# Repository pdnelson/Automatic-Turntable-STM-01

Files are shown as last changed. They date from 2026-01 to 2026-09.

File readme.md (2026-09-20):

# The Statimatic STM-01

This is (going to be) a fully-automatic, modular turntable, called the Statimatic STM-01. The development of this turntable is being documented in the following YouTube series: [https://www.youtube.com/watch?v=k4UXI1rkMYs\&list=PL\_8A3xK4AntYpp8yXHuAbhb6lULQ2ivFA](https://www.youtube.com/playlist?list=PL_8A3xK4AntYpp8yXHuAbhb6lULQ2ivFA)

At this time, an AR-XA turntable (left) is being used as the fill-in "turntable" for the STM-01 (right) during development. Eventually, the STM-01 will get its own turtable


## Electronics
This project is driven by a Teensy 4.1, three stepper motors to facilitate movement, multiplexers, a shift register, and more! See the `electrical` folder for the full schematic (so far).

Development is progressing on a breadboard, with questionable organization. Eventually, the plan is to etch a custom PCB.


### Schematic

This is the schematic as of 7 June 2026. The objective is to eliminate as much multiplexing as possible at the end of the project, if there are extra Teensy pins left over. The movement stepper demultiplexers (part `SN74LVC1G18DBVR`) will be the first to go. So far, it's looking like I may be able to eliminate these, as their use only saves me 3 pins. I'm not going to pull the trigger on this quite yet, though, because I may encounter other difficulties later on in the project, requiring the use of more pins. It's up in the air at this point.
schematic

## Mechanisms
The automatic tonerm's operation is facilitated by two mechanisms: One for vertical movement (right), and one for horizontal (left).

The vertical axis has a stepper motor driving movement, and a 10k slide potentiometer acting as an absolute encoder, so its position can be monitored.

The horizontal axis has a stepper motor driving horizontal movements, and another stepper motor to engage/disengage the horizontal motor for automatic movement. This mechanism is currently in progress, so there is some more work to do here.



## Previous Turntable
I designed a prototype turntable previously, separately from this repository, around late 2020/early 2021. That prototype lives in [another repository](https://github.com/pdnelson/Automatic-Record-Player). Though I'm no longer working on that project, much of the research, and many of the ideas I experimented with have made their way into this project.

## Planned Features
The built-in features of this turntable will be kept to a minimum, so that development can go more quickly. These features will be able to be expanded using the 5 expansion ports on the back of the turntable.

### Commands
Built-in, the plan is to have two commands: Play and pause. 

"Play" will move the tonearm from the "home" position to the outer edge of the record on the turntable. If the tonearm is not in the home position when "play" is pressed, then it will return home.

"Pause" will lift the tonearm up if it's set down, and set the tonearm down if it's lifted. "Up" movement will be quick, while "down" movement will be slow, to keep records from being damaged.

### Automatic pickup
The turntable will be able to automatically detect the end of the record, and pick itself up when it reaches that point.

### Size Selection
There will be four settings for size selection: 7", 10" and 12". The fourth option is "auto," where the turntable will use the built-in IR sensor to detect the record edge.

One caveat of using "auto" is that the record edge detection will likely be slower, while selecting a specific size will immediately know where to go.

### Speed Selection
There will be four settings for speed selection: 33 1/3, 45, and 78 RPM. The fourth option is "auto," where the turntable will guess, based on the record size, what speed you want.

For 12" records, the 33 1/3 RPM speed will be used. For 10" records, the 78 RPM speed will be used. For 7" records, the 45 RPM speed will be used. If an unusual size is detected, the fallback will be 78 RPM. Why? There are a lot of unusual 78-RPM record sizes out there, so I feel like this one's fitting.

### Statistics
The turntable will maintain a set of statistics that will be able to be viewed on the "Control Panel" module, or "Web Server" module.

These statistics could include:
- Current number of hours/minutes on the stylus
- How many records you've played
  - This will (likely) be counted by size and speed
- How long you've had the turntable powered on
- How long you've had the turntable playing a record

### Modularity

The plan is to allow connection of up to 5 external modules to the turntable, concurrently. The intention is to design the turntable as its own standalone unit, before any modules, so that each module can be designed in isolation.

mod-all-modules-clock

These could be, for example:
- Record flipper
- Record changer
- Second tonearm
- FM transmitter
- Preamp
- Alarm clock
- Remote control
- Splitter (to allow for even more modules!)
- Communication adapter to your favorite vintage computer from the '70s or '80s
- Control panel
- Web server

... And so on!

Got an idea for a module that you think would be cool? Send me a message; I might agree! Though I'm not developing any modules yet, it will be good to build up a nice list of things so I never run out of things to work on.

## Progress

This project has a lot of work that needs done to it. Here's what's been completed so far, and what's left to do:
- [x] Prototype documentation
- [x] Lift mechanism
- [x] Pause/unpause routine
- [x] Design pivoting mechanism
- [x] Design tonearm and headshell assembly
- [x] Connect tonearm to electronics
- [x] Status shift register
- [x] Command Button UI
- [x] Error handling
- [x] External Commands
- [x] Horizontal clutch mechanism
- [x] Horizontal position tracking
- [x] Calibration routine
- [x] "Specific Size" play routine
- [ ] IR record/track detection
- [ ] "Automatic" play routine
- [ ] Automatic homing routine
- [ ] Track forward/backward routine
- [ ] Headshell capacitive touch sensor
- [ ] Audio cut-off circuit
- [ ] Prototype motor/3-phase belt-driven turntable setup
- [ ] Speed monitoring routine
- [ ] Finalized turntable setup (heavy platter and big pulley)
- [ ] Design power supply
- [ ] Save settings when powered off
- [ ] Prototype plinth using plywood
- [ ] Finalized plinth using whatever material I decide to use
- [ ] Design PCB
- [ ] Etch PCB
- [ ] Celebrate a complete STM-01 turntable

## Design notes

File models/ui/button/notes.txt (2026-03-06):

Aluminum rod should be 12mm in length; 1/2" in diameter

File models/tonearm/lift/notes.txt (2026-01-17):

Must use, at most, 15mm layer height for tonearm-lift-attachment

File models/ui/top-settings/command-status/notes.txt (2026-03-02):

Use 0.15mm layers for all parts, except for the bottom mount.

Text:
- Font: Yu Gothic UI Semibold
- Height: 8.00mm
- Extruded: 0.0mm
- Form: Filled
- Weight: Bold

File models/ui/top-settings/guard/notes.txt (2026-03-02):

Model number text:
- Font: Bahnschrift SemiLight SemiConde
- Weight: Regular
- Form: Filled
- Height: 14mm
- Extruded: 0.0mm

Size/speed text:
- Same as above, except height: 5.0mm

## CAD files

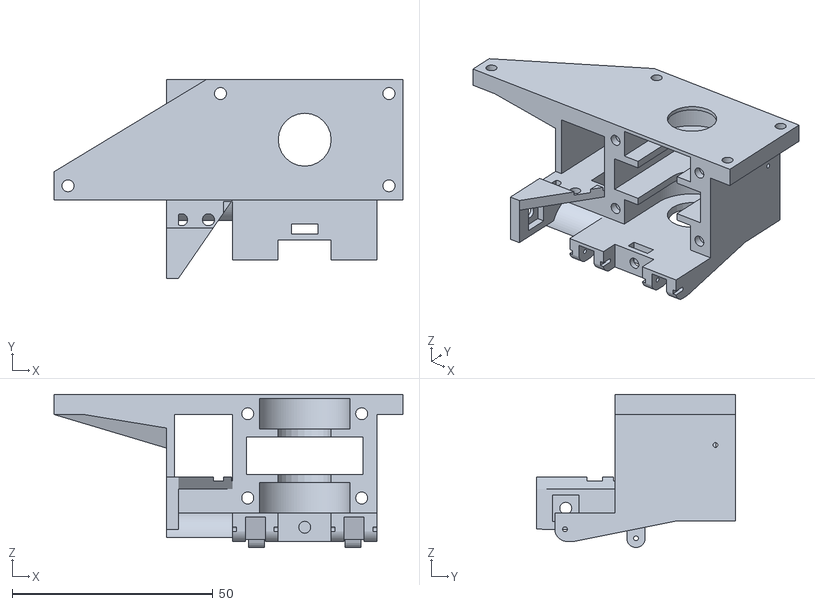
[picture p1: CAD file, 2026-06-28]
models/movement-hub/horizontal/horizontal-hub-main.stl
87.0 x 49.6 x 38.2

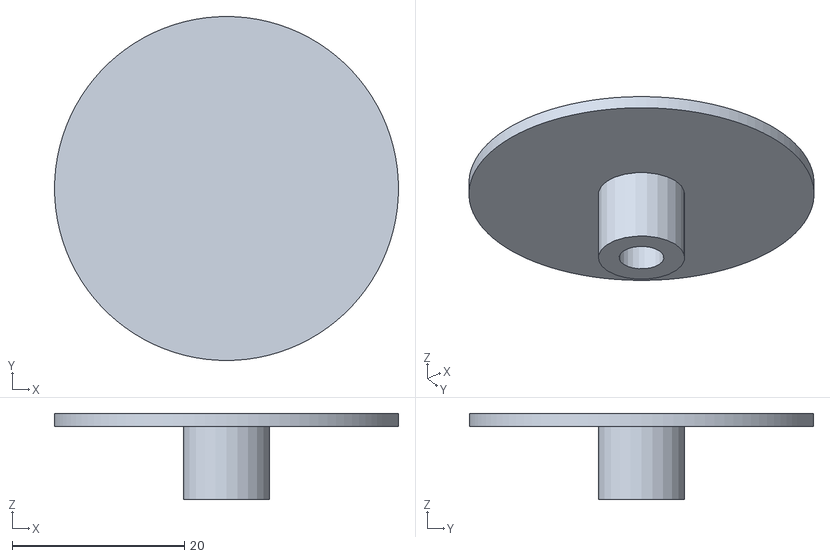
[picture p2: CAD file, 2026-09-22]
models/movement-hub/horizontal/horizontal-hub-motor-disc.stl
40.0 x 40.0 x 10.0

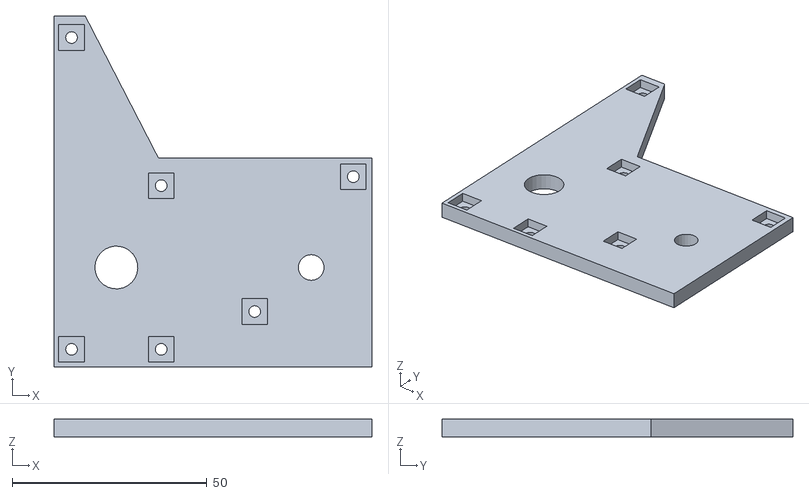
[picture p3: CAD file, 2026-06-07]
models/movement-hub/hub-mount.stl
81.6 x 90.0 x 4.50

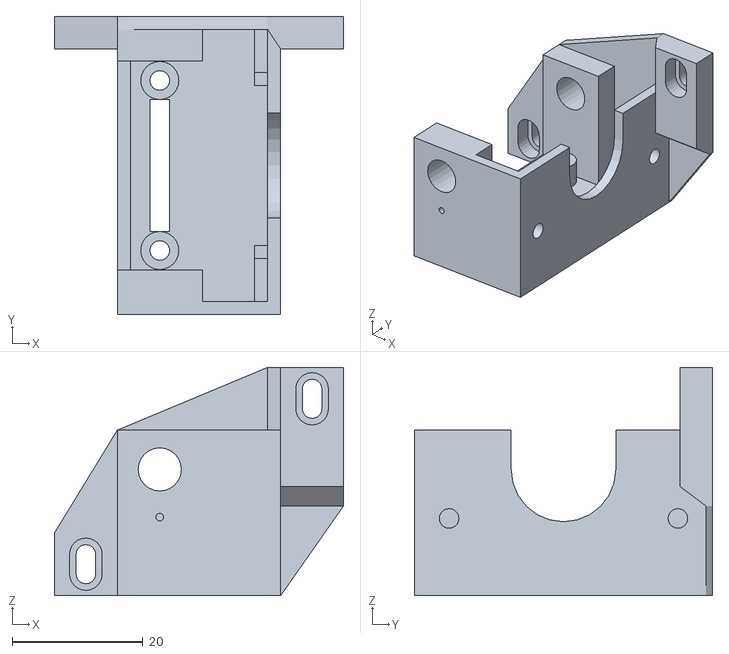
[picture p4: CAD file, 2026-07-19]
models/movement-hub/vertical/vertical-hub.stl
44.2 x 45.6 x 34.9

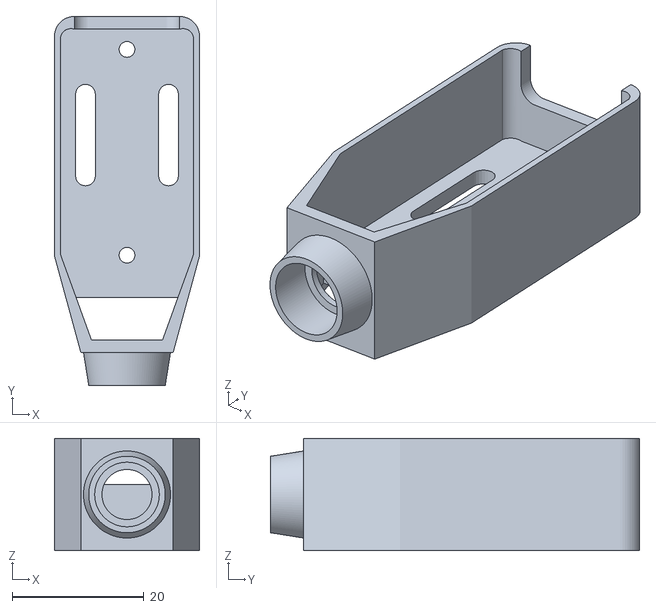
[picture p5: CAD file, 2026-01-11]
models/tonearm/headshell/headshell.stl
22.0 x 56.0 x 17.0

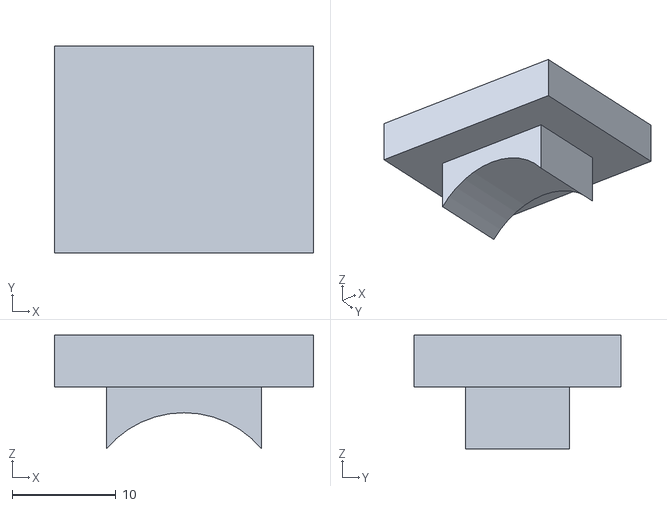
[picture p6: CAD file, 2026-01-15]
models/tonearm/headshell/lift-clamp/lift-clamp-top.stl
25.0 x 20.0 x 11.0

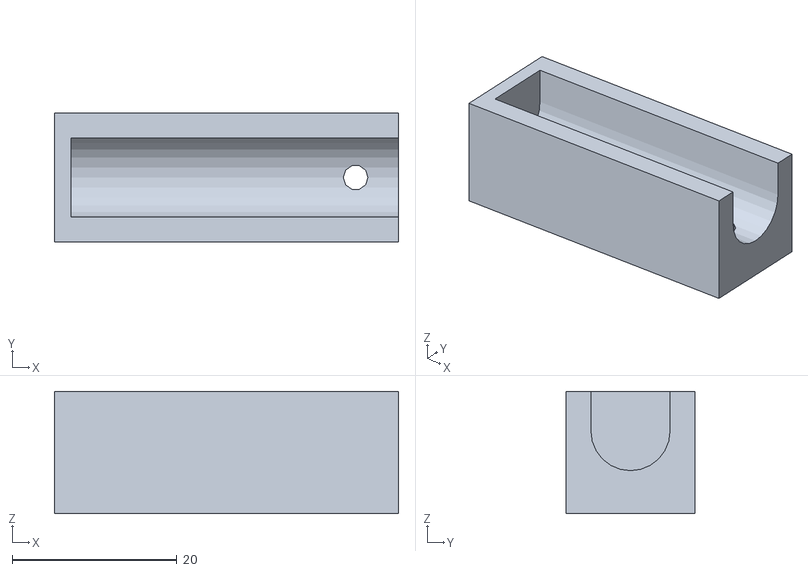
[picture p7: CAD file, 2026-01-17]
models/tonearm/lift/alignment/tonearm-lift-alignment-tool.stl
41.7 x 15.6 x 14.8

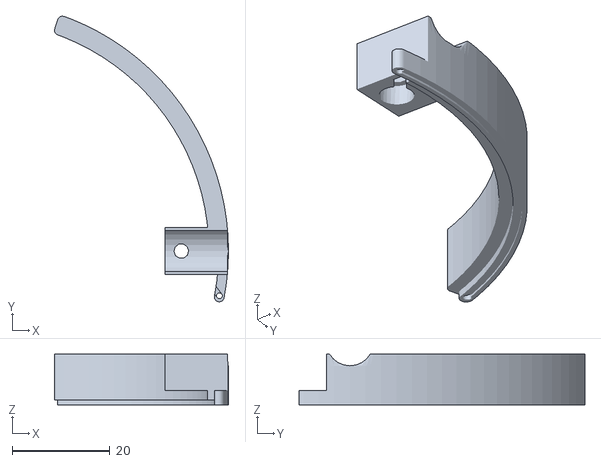
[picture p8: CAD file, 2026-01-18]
models/tonearm/lift/tonearm-lift-attachment.stl
35.5 x 58.3 x 10.4

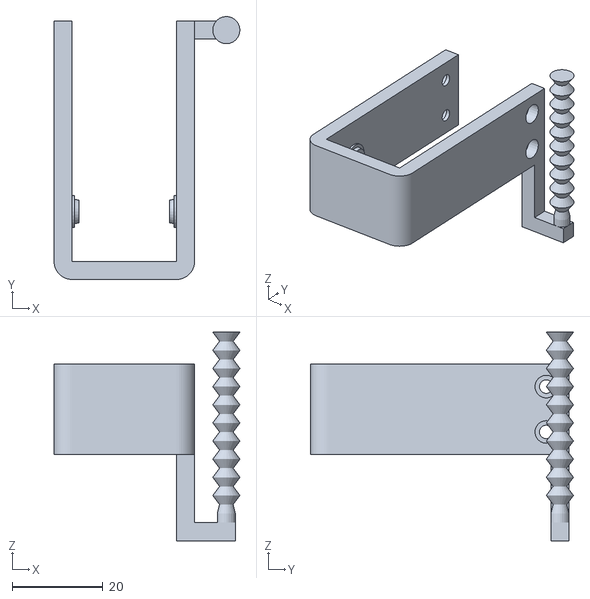
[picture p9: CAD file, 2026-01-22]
models/tonearm/pivot-mechanism/pivot-tonearm-holder.stl
41.0 x 58.0 x 46.0

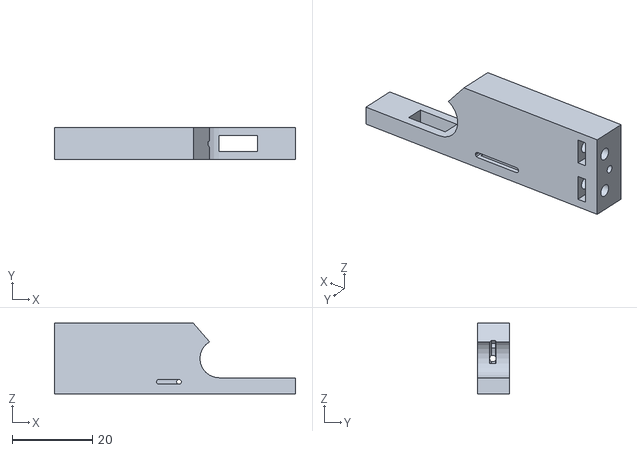
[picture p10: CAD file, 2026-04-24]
models/tonearm/rest/tonearm-rest.stl
60.0 x 7.90 x 17.6

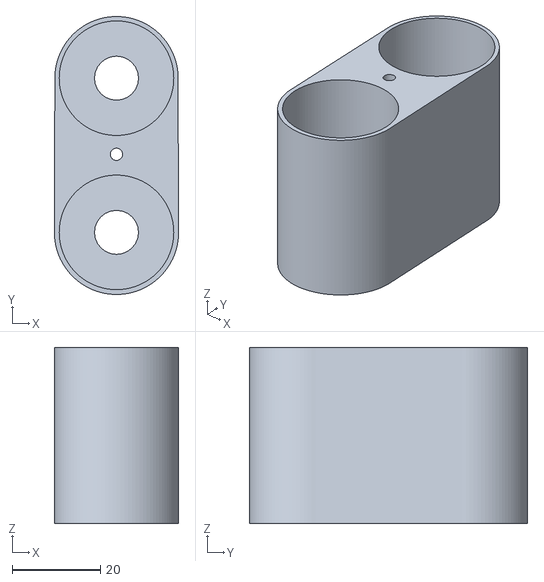
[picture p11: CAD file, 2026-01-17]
models/tonearm/weight/tonearm-weight.stl
28.2 x 63.1 x 40.0

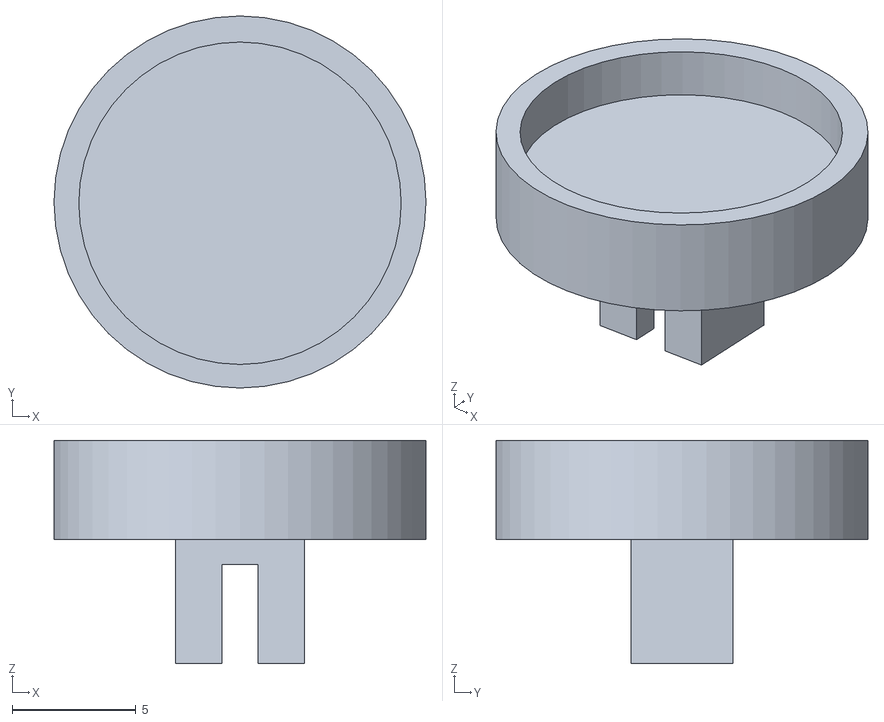
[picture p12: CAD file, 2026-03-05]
models/ui/button/button.stl
15.0 x 15.0 x 9.00

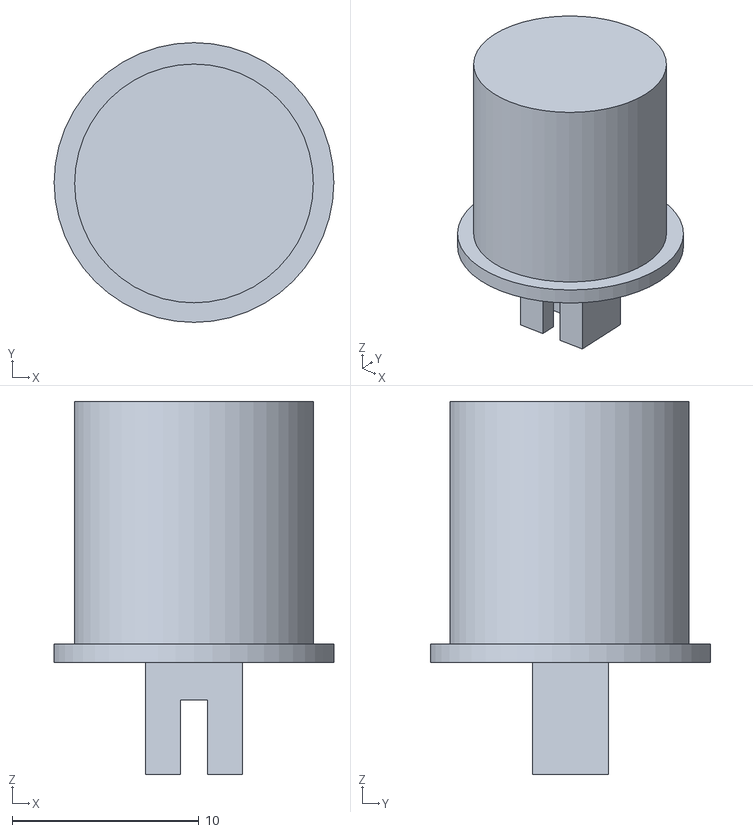
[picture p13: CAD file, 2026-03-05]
models/ui/button/prototype/button-prototype.stl
15.0 x 15.0 x 20.0

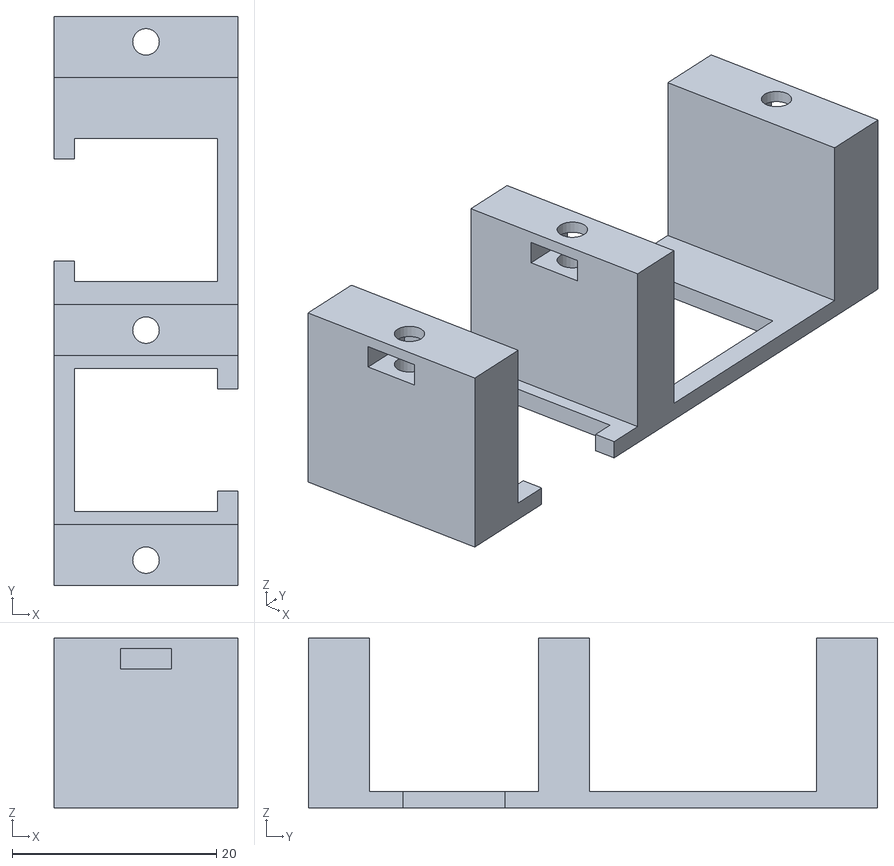
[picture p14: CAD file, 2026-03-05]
models/ui/top-settings/command-status/button/command-button-holder.stl
18.0 x 55.7 x 16.6

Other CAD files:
models/ui/top-settings/command-status/command-top-display-mount.stl
models/ui/top-settings/command-status/display/command-display-power.stl
models/ui/top-settings/guard/prototype/ui-guard-prototype-pt-2.stl
models/ui/top-settings/guard/ui-guard-without-text.dxf
models/movement-hub/horizontal/brackets-positioners/horizontal-hub-bearing-bracket.skp
models/movement-hub/horizontal/brackets-positioners/horizontal-hub-bearing-bracket.stl
models/movement-hub/horizontal/brackets-positioners/horizontal-hub-shaft-positioner.skp
models/movement-hub/horizontal/brackets-positioners/horizontal-hub-shaft-positioner.stl
models/movement-hub/horizontal/brackets-positioners/screw-contact-pad.skp
models/movement-hub/horizontal/brackets-positioners/screw-contact-pad.stl
models/movement-hub/horizontal/hinge-washer.skp
models/movement-hub/horizontal/hinge-washer.stl
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

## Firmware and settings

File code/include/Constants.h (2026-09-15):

#ifndef CONSTANTS_H

#define VERSION_MAJOR 0
#define VERSION_MINOR 0
#define VERSION_PATCH 1

#define SERIAL_COMMAND_INIT_KEY 0b00001100
#define SERIAL_COMMAND_MODEL_KEY 0b01101101 // 109 in decimal; 'm' in ASCII
#define SERIAL_COMMAND_CONNECTION_SUCCESS 0b10010010

#define SERIAL_ADVANCED_START_KEY 0b01010111
#define SERIAL_ADVANCED_END_KEY 0b10101000

// The speed at which serial devices should communicate with this turntable.
#define SERIAL_SPEED 115200

// The amount of time, in milliseconds, that a mux button must be held for the `ButtonResult::Held` status to be triggered.
#define BUTTON_HOLD_INTERVAL 2000

// The debounce interval, in milliseconds, for a mux button. I.e. the button cannot be pressed/released more than once within this duration.
#define BUTTON_DEBOUNCE_INTERVAL 20

// The interval, in microseconds, at which to poll the input multiplexer.
#define MUX_POLL_INTERVAL 100

// One seconds, in microseconds.
#define ONE_SECOND_MICROS 1000000

/**
 * Constants related to the pause/unpause commands -------------
 */

// A margin of error for the slide potentiometer "encoders."
#define VERTICAL_ENCODER_TOLERANCE 5

// The number of encoder ticks to move the tonearm down after contact with the lift has been terminated.
#define TICKS_BELOW_RECORD 15 // Set to 0 because the debounce ends up doing this well enough for now (or forever, maybe)

// The pause status is determined by the upper limit, and this is the margin of error for what can be considered "paused"
#define PAUSE_ERROR 50

// The amount of time, in microseconds, that must pass between status changes of the lift.
#define LIFT_DEBOUNCE_MICROS 50000

// The amount of time, in microseconds, that must pass between status changes of the home stand.
#define HOME_DEBOUNCE_MICROS 100000

// The number of steps the vertical stepper must reach before it is considered "stalled".
#define VERTICAL_STALL_STEPS 100

// If the tonearm is hovering over the "home" position, it should go down quickly, as opposed to slowly. This threshold
// helps determine if it's over "home".
#define HOME_THRESHOLD 100



// When the tonearm lifts up toward the center of the platter, it might bounce a little bit. This timeout represents the maximum
// amount of time we allow for the tonearm to bounce, before it should level out.
#define LIFT_BOUNCE_TIMEOUT_MICROS 1750000

// How fast the tonearm should move when lifting.
#define LIFT_UP_SPEED 10

// How fast the tonearm should move when being set down gently.
#define SET_DOWN_SLOWLY 3

// How fast the tonearm should move when being set down quickly.
#define SET_DOWN_QUICKLY 14

/**
 * Constants related to the horizontal movement -----------
 */

// The RPM at which the clutch stepper spins.
#define CLUTCH_SPEED 14

// The number of steps for the clutch to engage, after the limit switch is released.
#define CLUTCH_ENGAGE_STEPS 250

// If the clutch switch doesn't release after this number of steps, the clutch movement failed.
// Similarly, if the clutch switch doesn't press after this value + CLUTCH_ENGAGE_STEPS, the clutch movement failed.
#define CLUTCH_TIMEOUT_STEPS 100

/**
 * Calibration constants
 */

// The number of encoder ticks above the upper threshold that the turntable should move. This value is applied at the time of calibration.
#define VERTICAL_BOUNDARY_UPPER_BUFFER 80

// The number of encoder ticks below the lower threshold that the turntable should move. This value is applied at the time of calibration.
#define VERTICAL_BOUNDARY_LOWER_BUFFER 30

// When zeroing the azimuth encoder, this is the INITIAL offset when beginning the calibration routine. This value is compatible with an incorrect polarity,
// because it's pretty close to the middle of both bounds.
#define HOME_ZERO_OFFSET 8000

/**
 * Below here are Serial aliases to make it easier to identify the STM-01's serial ports on the back in the code.
 */

#define STM_SERIAL_USB Serial
#define STM_SERIAL_1 Serial1
#define STM_SERIAL_2 Serial2
#define STM_SERIAL_3 Serial7
#define STM_SERIAL_4 Serial8
#define STM_SERIAL_5 Serial3

#endif

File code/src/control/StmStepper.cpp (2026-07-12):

#include <StmStepper.h>
#include <Arduino.h>
#include <Pin.h>
#include <AzimuthDirection.h>
#include <StmStepperResult.h>

StmStepper::StmStepper(Pin pin1, Pin pin2, Pin pin3, Pin pin4) {
    this->pin1 = pin1;
    this->pin2 = pin2;
    this->pin3 = pin3;
    this->pin4 = pin4;

    pinMode(pin1, OUTPUT);
    pinMode(pin2, OUTPUT);
    pinMode(pin3, OUTPUT);
    pinMode(pin4, OUTPUT);
}

void StmStepper::setSpeed(uint8_t speedRpm) {
    this->topSpeedTimeBetweenStepsMicros = 60000000L / STEPPER_STEPS_PER_REVOLUTION / speedRpm;
}

void StmStepper::setDirection(int8_t direction) {
    this->direction = direction;
}

void StmStepper::setRampUpEncoderTicks(uint16_t rampUp) {
    rampUpEncoderTicks = rampUp;
}

void StmStepper::setRampDownEncoderTicks(uint16_t rampDown) {
    rampDownEncoderTicks = rampDown;
}

void StmStepper::setEncoderRange(uint16_t start, uint16_t end, uint8_t tolerance) {
    startEncoderPosition = start;
    destinationEncoderPosition = end;
    destinationEncoderPositionTolerance = tolerance;
    direction = (start > end) ? AzimuthDirection::Clockwise : AzimuthDirection::CounterClockwise;
}

StmStepperResult StmStepper::step(unsigned long clockMicros, uint16_t currentEncoderPosition) {
    StmStepperResult result = StmStepperResult();

    // The movement has completed.
    if(movementCompleted(currentEncoderPosition)) {
        result.movementCompleted = true;
    } 
    
    // The movement has not completed, and we need to take a step.
    else {
        uint16_t speed = topSpeedTimeBetweenStepsMicros;

        // Ramp down calculation
        // prioritize ramp down since that's the functional one; ramp up just looks pretty
        if(rampingDown(currentEncoderPosition)) {
            speed = rampDownSpeed(currentEncoderPosition);
        }

        // Ramp up calculation
        else if(rampingUp(currentEncoderPosition)) {
            speed = rampUpSpeed(currentEncoderPosition);
        }

        if(clockMicros - lastStepMicros > speed) {
            performStep();
            lastStepMicros = clockMicros;
            result.stepTaken = true;
        }
    }


    return result;
}

bool StmStepper::stepBlind(unsigned long clockMicros) {
    if(clockMicros - lastStepMicros > topSpeedTimeBetweenStepsMicros) {
        performStep();
        lastStepMicros = clockMicros;
        return true;
    }

    return false;
}

void StmStepper::releaseMotorCurrent() {
    lastStepMicros = 0;
    digitalWrite(pin1, LOW);
    digitalWrite(pin2, LOW);
    digitalWrite(pin3, LOW);
    digitalWrite(pin4, LOW);
}

bool StmStepper::rampingDown(uint16_t currentEncoderPosition) {
    bool movingNegative = destinationEncoderPosition < startEncoderPosition;

    return (movingNegative && currentEncoderPosition - rampDownEncoderTicks < destinationEncoderPosition) ||
            (!movingNegative && currentEncoderPosition + rampDownEncoderTicks > destinationEncoderPosition);
}

bool StmStepper::rampingUp(uint16_t currentEncoderPosition) {
    bool movingNegative = destinationEncoderPosition < startEncoderPosition;

    return (movingNegative && currentEncoderPosition > startEncoderPosition - rampUpEncoderTicks) ||
            (!movingNegative && currentEncoderPosition < startEncoderPosition + rampUpEncoderTicks);
}

uint16_t StmStepper::rampDownSpeed(uint16_t currentEncoderPosition) {
    uint16_t ticksSoFar = 0; // todo
    return ((STEPPER_MAX_DELAY_BETWEEN_STEPS - topSpeedTimeBetweenStepsMicros) / rampDownEncoderTicks) * ticksSoFar;
}

uint16_t StmStepper::rampUpSpeed(uint16_t currentEncoderPosition) {
    uint16_t ticksSoFar = 0; // todo
    return ((STEPPER_MAX_DELAY_BETWEEN_STEPS - topSpeedTimeBetweenStepsMicros) / rampDownEncoderTicks) * ticksSoFar;
}

bool StmStepper::movementCompleted(uint16_t currentEncoderPosition) {
    bool movingNegative = destinationEncoderPosition < startEncoderPosition;
    
    return (movingNegative && currentEncoderPosition - destinationEncoderPositionTolerance < destinationEncoderPosition) ||
        (!movingNegative && currentEncoderPosition + destinationEncoderPositionTolerance > destinationEncoderPosition);
}

void StmStepper::performStep() {
    currentStep += direction;

    if(currentStep == 4) {
        currentStep = 0;
    } else if(currentStep == -1) {
        currentStep = 3;
    }

    switch (currentStep) {
        case 0:
            digitalWrite(pin1, HIGH);
            digitalWrite(pin2, LOW);
            digitalWrite(pin3, HIGH);
            digitalWrite(pin4, LOW);
            break;
        case 1:
            digitalWrite(pin1, LOW);
            digitalWrite(pin2, HIGH);
            digitalWrite(pin3, HIGH);
            digitalWrite(pin4, LOW);
            break;
        case 2:
            digitalWrite(pin1, LOW);
            digitalWrite(pin2, HIGH);
            digitalWrite(pin3, LOW);
            digitalWrite(pin4, HIGH);
            break;
        case 3:
            digitalWrite(pin1, HIGH);
            digitalWrite(pin2, LOW);
            digitalWrite(pin3, LOW);
            digitalWrite(pin4, HIGH);
            break;
    }
}

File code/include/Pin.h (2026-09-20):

#include <Arduino.h>

#ifndef PIN_H
#define PIN_H

enum Pin : uint8_t {
    Serial1Rx = 0,
    Serial1Tx = 1,
    InputMuxA = 2,
    InputMuxB = 3,
    InputMuxC = 4,
    InputMuxResult = 5,
    MovementStep4 = 6,
    Serial2Rx = 7,
    Serial2Tx = 8,
    MovementStep3 = 9,
    MovementStep2 = 10,
    MovementStep1 = 11,
    HorizontalStep = 12,
    PowerOnStatusIn = 13,
    Serial5Tx = 14,
    Serial5Rx = 15,
    SpeedEncoderB = 16,
    SpeedEncoderA = 17,
    HeadshellPhotoDiode = 18,
    TurntableMotorPhase3 = 19,
    TurntableMotorPhase2 = 20,
    TurntableMotorPhase1 = 21,
    HorizontalClutchSwitch = 22,
    VerticalPosition = 23,
    ReservedI2CScl = 24, // Wire2
    ReservedI2CSda = 25, // Wire2
    HorizontalEnable = 26,
    HorizontalDirection = 27,
    Serial3Rx = 28,
    Serial3Tx = 29,
    Lift = 30,
    HorizontalSleep = 31,
    Serial4Rx = 34,
    Serial4Tx = 35,
    HorizontalClutchStep4 = 38,
    HorizontalClutchStep3 = 39,
    HorizontalClutchStep2 = 40,
    HorizontalClutchStep1 = 41,

    // Unused pins
    Unused32 = 32,
    Unused33 = 33,
    Unused36 = 36,
    Unused37 = 37
};

#endif

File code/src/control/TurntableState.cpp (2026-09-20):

#include <TurntableState.h>
#include <Arduino.h>
#include <CommandResult.h>
#include <Constants.h>
#include <HomeStatus.h>
#include <InputMux.h>
#include <LiftStatus.h>
#include <memory>
#include <MuxPin.h>
#include <Pin.h>
#include <RecordSize.h>
#include <StmBasicStepper.h>
#include <StmShift.h>
#include <TurntableSpeed.h>
#include <CmdError.h>
#include <CmdPause.h>
#include <CmdUnPause.h>
#include <CmdProtoPlay.h>
#include <StmEncoder.h>
#include <ClutchStatus.h>
#include <StmPolarity.h>
#include <CmdGoToPositionH.h>
#include <CmdCalibration.h>

TurntableState::TurntableState() : 
    outputShift(Pin::ReservedI2CSda, Pin::ReservedI2CScl),
    serialComm(this),
    inputMux(Pin::InputMuxA, Pin::InputMuxB, Pin::InputMuxC, Pin::InputMuxResult, MUX_POLL_INTERVAL, BUTTON_HOLD_INTERVAL, BUTTON_DEBOUNCE_INTERVAL),
    verticalStepper(Pin::MovementStep1, Pin::MovementStep3, Pin::MovementStep2, Pin::MovementStep4),
    clutchStepper(Pin::HorizontalClutchStep1, Pin::HorizontalClutchStep3, Pin::HorizontalClutchStep2, Pin::HorizontalClutchStep4),
    azEncoder(Pin::ReservedI2CSda, Pin::ReservedI2CScl),
    horizontalStepper(azEncoder, Pin::HorizontalSleep, Pin::HorizontalEnable, Pin::HorizontalStep, Pin::HorizontalDirection),
    calibration(),
    settings()
{
    pinMode(Pin::VerticalPosition, INPUT);
    pinMode(Pin::HorizontalClutchSwitch, INPUT_PULLUP);

    // Lift
    pinMode(Pin::Lift, INPUT_PULLUP);
    lastLiftStatus = digitalRead(Pin::Lift);

    // Turn on the power LED
    outputShift.setValue(StmShiftPin::LedPower, true);

    settings.load();

    updateCustomSpeed(settings.speed);
    updateSize(settings.size);

    clutchStepper.setSpeed(CLUTCH_SPEED);

    calibration.load();

    azEncoder.setPolarity(calibration.polarityH);
    azEncoder.zeroOutEncoder(calibration.azEncoderOffset);
    horizontalStepper.setPolarity(calibration.hStepperPolarity);
    horizontalStepper.sleep();
}

void TurntableState::monitor() {
    updateClockMicros();
    advanceCounts();
    serialComm.monitor();
    monitorCommandInput();
    executeCommand();
    azEncoder.monitor(clockMicros);

    // Output statuses
    blinkCustomSpeedIndicator();
    outputShift.monitor();
}

void TurntableState::executeCommand() {
    if(currentCommand != nullptr) {
        CommandResult result = currentCommand->execute();

        if(result == CommandResult::Success) {

            // When coming out of the calibration command, go home (if we aren't already there)
            if(currentCommand->getCommandId() == CommandId::Calibration && getHomeStatus() != HomeStatus::Homed) {
                currentCommand = std::make_unique<CmdGoToPositionH>(this, calibration.home, 10, 14);
            } else {
                currentCommand = nullptr;
            }
        } else if(result > CommandResult::Success) {
            currentCommand = std::make_unique<CmdError>(this, result);
        }
    }
}

void TurntableState::rotateSpeed() {
    switch(selectedSpeed) {
        case TurntableSpeed::Rpm33:
            updateSpeed(TurntableSpeed::Rpm45);
            break;
        case TurntableSpeed::Rpm45:
            updateSpeed(TurntableSpeed::Rpm78);
            break;
        case TurntableSpeed::Rpm78:
            updateSpeed(TurntableSpeed::RpmAuto);
            break;
        case TurntableSpeed::RpmAuto:
            updateSpeed(TurntableSpeed::Rpm33);
            break;
        case TurntableSpeed::RpmCustom:
            updateSpeed(TurntableSpeed::Rpm33);
            break;
    }
}

LiftStatus TurntableState::getLiftStatus() {
    bool status = digitalRead(Pin::Lift);

    if(status == lastLiftStatus) {
        liftDebounce = clockMicros;
        return (LiftStatus) status;
    } else if(clockMicros - liftDebounce > LIFT_DEBOUNCE_MICROS) {
        lastLiftStatus = status;
        return (LiftStatus) status;
    } else {
        return (LiftStatus) !status;
    }
}

HomeStatus TurntableState::getHomeStatus() {
    uint16_t difference = abs((int16_t)azEncoder.getNormalizedPosition() - (int16_t)calibration.home);

    if(difference <= HOME_THRESHOLD) {
        return HomeStatus::Homed;
    }

    return HomeStatus::NotHomed;
}

uint16_t TurntableState::getVerticalEncoderPos() {
    if(calibration.polarityV == StmPolarity::Normal) {
        return analogRead(Pin::VerticalPosition);
    } else {
        return V_ENCODER_MAX_VALUE - analogRead(Pin::VerticalPosition);
    }
}

bool TurntableState::isPaused() {
    return getVerticalEncoderPos() >= (calibration.verticalUpperLimit - PAUSE_ERROR);
}

ClutchStatus TurntableState::clutchEngaged() {
    return (ClutchStatus)digitalRead(Pin::HorizontalClutchSwitch);
}

void TurntableState::updateCustomSpeed(float newSpeed) {
    if(newSpeed < 33.33333 && newSpeed > 33.3) {
        updateSpeed(TurntableSpeed::Rpm33);
    } else if(newSpeed == 45.0) {
        updateSpeed(TurntableSpeed::Rpm45);
    } else if(newSpeed == 78.0) {
        updateSpeed(TurntableSpeed::Rpm78);
    } else if(newSpeed == 0.0) {
        updateSpeed(TurntableSpeed::RpmAuto);
    } else {
        settings.speed = newSpeed;
        updateSpeed(TurntableSpeed::RpmCustom);
    }
}

void TurntableState::updateSpeed(TurntableSpeed newSpeed) {
    // First set all speed LEDs to off
    outputShift.setValue(StmShiftPin::Led78Rpm, false);
    outputShift.setValue(StmShiftPin::Led45Rpm, false);
    outputShift.setValue(StmShiftPin::Led33Rpm, false);
    outputShift.setValue(StmShiftPin::LedAutoSpeed, false);

    switch(newSpeed) {
        case TurntableSpeed::Rpm33:
            settings.speed = 33.3333;
            outputShift.setValue(StmShiftPin::Led33Rpm, true);
            break;
        case TurntableSpeed::Rpm45:
            settings.speed = 45.0;
            outputShift.setValue(StmShiftPin::Led45Rpm, true);
            break;
        case TurntableSpeed::Rpm78:
            settings.speed = 78.0;
            outputShift.setValue(StmShiftPin::Led78Rpm, true);
            break;
        case TurntableSpeed::RpmAuto:
            // TODO: If playing a record, go based on the last-played size

            outputShift.setValue(StmShiftPin::LedAutoSpeed, true);
            break;
        case TurntableSpeed::RpmCustom:
            /* do nothing */
            break;
    }

    selectedSpeed = newSpeed;
    customSpeedIndicatorCounter = clockMicros;
}

void TurntableState::rotateSize() {
    switch(settings.size) {
    case RecordSize::In7:
        updateSize(RecordSize::In10);
        break;
    case RecordSize::In10:
        updateSize(RecordSize::In12);
        break;
    case RecordSize::In12:
        updateSize(RecordSize::InAuto);
        break;
    case RecordSize::InAuto:
        updateSize(RecordSize::In7);
        break;
    }
}
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

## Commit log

2025-11-27 Remove earlier revisions of vertical movement
    [cap-pulley.skp, cap-pulley.stl, motor-arm.skp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]
2025-11-27 Update and shift serial pins on Teensy
2025-11-29 Finish output pin implementation in InputMux class
2025-11-30 Add more comments and fix bug with tonearm lowering
    [Constants.h]
2025-12-01 Update vertical movement to accommodate wire placement
    [rod-cap.skp, rod-cap.stl, vertical-hub.skp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]
2025-12-01 Update schematic mux IC voltages to 3.3v
2025-12-01 Implement OnHold button event
2025-12-07 Update prototype documentation to represent current plan
2025-12-11 Fix typo and mention fallback to 78 RPM
2026-01-10 Implement gimbal tonearm mechanism models
    [headshell-stencil.skp, headshell-stencil.stl, headshell.skp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]
2026-01-11 Move tonearm-coupler to more-appropriate folder
    [tonearm-coupler.skp, tonearm-coupler.stl]
2026-01-11 Update headshell to have room for more wires
    [headshell-stencil.skp, headshell-stencil.stl, headshell.skp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]
2026-01-15 Implement tonearm rest and anti-skate
    [horizontal-hub.skp, horizontal-hub.stl, lift-clamp-bottom.skp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]
2026-01-16 Redesign tonearm rest
    [BOM.xlsx, tonearm-rest-latch.skp, tonearm-rest-latch.stl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]
2026-01-17 Implement tonearm lift
    [tonearm-lift-alignment-tool.skp, tonearm-lift-alignment-tool.stl, tonearm-lift-attachment.skp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]
2026-01-17 Add tonearm weight model to house aluminum
    [tonearm-weight.skp, tonearm-weight.stl]
2026-01-17 Remove nut hole from weight holder
    [tonearm-weight.skp, tonearm-weight.stl]
2026-01-17 Expand nut holes of tonearm rest
    [tonearm-rest.skp, tonearm-rest.stl]
2026-01-17 Expand nut holes of pivot base
    [pivot-base.skp, pivot-base.stl]
2026-01-17 Remove nut hole from tonearm weight holder
    [tonearm-weight.skp]
2026-01-18 Add more thickness to lift to prevent bouncing when lifting
    [tonearm-lift-attachment.skp, tonearm-lift-attachment.stl]
2026-01-19 Improve pivot tonearm holder tolerances
    [pivot-tonearm-holder.skp, pivot-tonearm-holder.stl]
2026-01-22 Update tolerances of tonearm holder
    [pivot-tonearm-holder.skp, pivot-tonearm-holder.stl]
2026-02-10 Flesh out shift register more on schematic
2026-02-13 Add fade circuit to command LEDs
2026-02-15 Remove Serial.prints that I accidentally committed
2026-03-02 Add user interface models
    [command-display-pause.skp, command-display-pause.stl, command-display-play.skp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]
2026-03-02 Update aerial model to account for user interface
    [turntable-aerial-model.skp]
2026-03-02 Flesh out schematic with output statuses
2026-03-02 Identify new unused pin on mux
2026-03-02 Rearrange MuxPin entries to match schematic changes
2026-03-05 Finalize UI and dimensions
    [button-prototype.skp, button-prototype.stl, command-button-holder.skp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]
2026-03-05 Finish button UI
    [button.skp, button.stl]
2026-03-06 Split out UI guard for laser etching
    [ui-guard-text-only.dxf, ui-guard-text-only.skp, ui-guard-without-text.dxf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]
2026-03-06 Implement error command - not yet used
    [Constants.h]
2026-03-07 Implement check for vertical stall
    [Constants.h]
2026-03-07 Update error to show binary code on speed/size LEDs
2026-03-07 Reorder UI buttons to match new layout
2026-03-13 Fix schematic pinout
2026-03-15 Fix and add more commands
    [ExternalCommand.h]
2026-03-23 Add UI display mounts
    [command-top-display-mount.skp, command-top-display-mount.stl, speed-size-top-display-mount.skp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]
2026-04-01 Add audio cut-off to to do list
2026-04-01 Add power supply to checklist
2026-04-02 Add numbers to schematic ICs
2026-04-24 Thicken display mounts
    [command-top-display-mount.skp, command-top-display-mount.stl, speed-size-top-display-mount.skp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]
2026-04-24 Extend holes in tonearm rest
    [tonearm-rest.skp, tonearm-rest.stl]
2026-04-25 Check off "Command Button UI"
2026-04-27 Fix lift bounce bug
    When lifting the tonearm while it's positioned toward the center of the
    platter, it would bounce a bit, triggering a failure when executing the
    "pause" command. The remedy for this was, instead of checking once at
    the end of the routine if the tonearm is lifted, wait n seconds after
    the routine has completed for it to show as lifted. If it times out,
    then the command will fail as it did before. In this commit, I give it
    1.5 seconds to normalize out, which should be plenty of time.
    [Constants.h]
2026-05-03 Temporarily wire up speed/size to jog horizontal stepper
2026-05-03 Implement prototype clutch parts
    [clutch-disc-motor.skp, clutch-disc-motor.stl, clutch-disc-shaft.skp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]
2026-05-05 Update horizontal models to accommodate prototype clutch engage/disengage
    [clutch-disc-motor.skp, clutch-disc-motor.stl, clutch-disc-shaft.skp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]
2026-05-05 Unhide horizontal hub
    [horizontal-hub.skp]
2026-05-14 Implemented functioanl clutch mechanism
    [horizontal-hub-engager.stl, horizontal-hub-main.stl, horizontal-hub-motor-holder.stl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]
2026-05-15 Update schematic to accommodate clutch changes
2026-05-15 Add prototype code to test clutch mechanism
2026-05-15 Update hub mount to accommodate horizontal updates
    [hub-mount.skp, hub-mount.stl]
2026-05-20 Implement prototype play routine for testing
2026-05-28 Fix sizing of hub shaft positioner so there is no vertical play in tonearm
    [horizontal-hub-shaft-positioner.skp, horizontal-hub-shaft-positioner.stl]
2026-05-31 Try to fix syntax anomalies to make this compile
    [CommandResult.h]
2026-05-31 Remove type from enums and replace circular TurntableState dependency
    [CommandResult.h, ExternalCommand.h]
2026-06-02 Fix Command design pattern implementation
    [StmShiftPin.h]
2026-06-03 Reorganize more files and fix commands
    [CommandResult.h, Constants.h, TurntableState.cpp]
2026-06-04 Implement command chaining
2026-06-06 Fix wrong enum being used when stalling moving down
2026-06-07 Update hub mount to match new horizontal movement layout
    [hub-mount.skp, hub-mount.stl]
2026-06-07 Add schematic to readme
2026-06-17 Make stall detection more reliable
2026-06-17 Allow vertical hub positioning to be adjustable
    [vertical-hub.skp, vertical-hub.stl]
2026-06-17 do something to schematic
2026-06-22 Remove unused components from schematic/code
2026-06-25 Update schematic to reflect hall effect sensor addition, replacing optical sensor
2026-06-25 Update schematic on readme
2026-06-25 Rename Wire2 SDA and SCL to be generic
2026-06-26 Implement untested encoder logic
2026-06-27 Fix StmEncoder not grabbing data correctly
    [StmEncoder.cpp]
2026-06-28 Accommodate sensor PCB in horizontal hub
    [horizontal-hub-hinge.stl, horizontal-hub-main.stl, horizontal-hub-motor-disc.stl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]
2026-06-30 Finalize horizontal hub models with position tracking
    [horizontal-hub-motor-holder.stl, horizontal-hub-sensor-holder.stl, horizontal-hub.skp]
2026-06-30 throw out value 0 in encoder data so it doesn't distort average
    [StmEncoder.cpp]
